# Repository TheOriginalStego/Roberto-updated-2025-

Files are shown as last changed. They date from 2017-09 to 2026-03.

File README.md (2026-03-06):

# Roberto

Roberto during Vivapoly 2014

This is the program that runs in Roberto, the pastis serving robot of [Robopoly](http://robopoly.epfl.ch) made by Steven Roelofsen.

The program runs on a white version of the [PRismino](https://github.com/Robopoly/PRismino) that is attached to the front of the robot. It needs the [`robopolyLCD`
](https://github.com/Robopoly/LCD-module) library for the LCD.

## Configuration

The program has been made so the robot could be configured live via the USB port, options that can be changed are: quantity of poured liquid, type of liquid (pastis or syrup) and method of serving (immediate or wait for button press).

There are 2 configurations for the robot, it usually server either syrup during non-alcoholic manifestations and then pastis during Vivapoly, the last big event of an academic year at EPFL.

Configuration commands:

| Command | Action | Parameters 			|
|---|---|---|
| 1 | Set new pouring weight | n (pouring weight in g, int) 			|
| 2 | Check configuration | 			|
| 3 | Read how many times the pump has been activated | 			|
| 4 | Show sensor values | 			|
| 5 | Change mode | 0 = automatic, 1 = manual 			|
| 6 | Change type | 0 = Ricard, 1 = syrup (unused) 	|
| 7 | Enable debug mode | 			|

So for example to set the pouring time the user first sends `1` to select the command and then sends the pouring time in milliseconds (ex: `2000`).

## Memory

Some information is stored in EEPROM to save it even when the robot is power cycled: drinks served, pouring time in milliseconds, serving type and serving mode. Drinks served and pouring time can be consulted at any time by pushing on the arm touch sensor on the right arm, the values will be shown on the front LCD.

## State machine

The program follows strictly a simple state machine that is very easy to manage:

Roberto finite state machine

In idle mode, while waiting for a cup to be inserted or removed, it moves and toggles its various servomotors and lights randomly to attract attention.

## Debug mode

The debug mode allows to enter a special mode that lets the user toggle on or off the lights, pump and show the sensor status on the LCD screen. To exit this mode the MCU has to be reset using the on-board button in front of the robot.

## Hardware design

The ears and hands are 3d printed. Only the ears are available as the others have gone lost (or unusable designs). The ears are identical and can easily be 3d printed.

The power system has been revised in May 2016, leading to the design of a new pump drive PCB featuring a MOSFET transistor. DC 5V regulation is now performed by Robopoly’s Power-Board instead of not-so-efficient linear regulators.

In 2017, a second pump was added. The pumps are driven by having stacked PCBs from 2016. Furthermore, a shield made from veroboard was made. It works as a normal shield instead of an "inverted shield". This way if the Prismino dies, any other can be used. 
Also, the amount of liquid to be poured is now measured using a scale instead of a timer (ie no measurement). This required the hand to be redesigned and the design can be found on the Fusion360 account of Robopoly.

## CHANGELOG
### 2025 Maintenance and repair
In may 2025, repair and maintenance was done by Tibor Truong.
The design of both hands was modified in order to adapt to various sizes of glasses and improve reliability. The loadcell was removed from it's plattform underneath the cup holder and was integrated directly into the cup holder (holder itself measures the weight). The hand on the "pouring" side was also redesigned. The hoses can now be installed and removed way faster thanks to zipties.
The switch that sensed the closing of the hands was replaced by a reed sensor. This ensures that contact is closed even when the arms don't touch very well (due to mechanical play).
The existing two pumps were thoroughly cleaned with a 1% NaOH solution to get rid of the mold and other gunk that has been building up for years.
During repair, the loadcell amplifier board was damaged, it got replaced by a more recent model sold by Robopoly.

Note for users: Please always rince the hoses at least with warm water (or better with a desinfecting solution) and dry them completely before putting away the robot for storage. Leaving liquids in the pumps and hoses leads to mold formation and it's very work intensive to get rid of it again. Not even mentioning that it's disgusting and not foodsafe.

## Credits

This project has been an ongoing one and a lot of people have been working on it without whom this wonderful robot would've never existed.

| Contribution | Name 										|
|---|---|
| Creator | Steven Roelofsen 										|
| Programmers | Karl Kangur, Taavet Kangur, Patrick Bobbink								|
| Electronics | Marco Pagnamenta, Benjamin Bonnal, Paul-Edouard Sarlin, Patrick Bobbink 	|
| Cabling, mechanics | Lobsang Blanchard, Patrick Bobbink				 				|

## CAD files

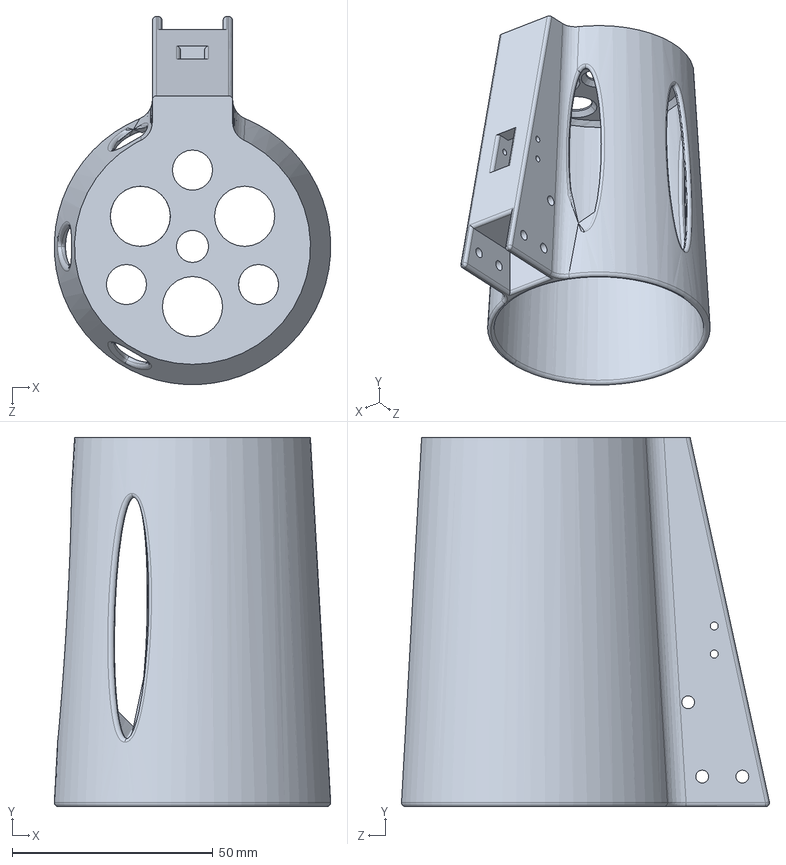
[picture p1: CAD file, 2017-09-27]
Hardware/Hand_second_version/sld/main_verre1.SLDPRT
68.8 x 92.0 x 91.7 mm

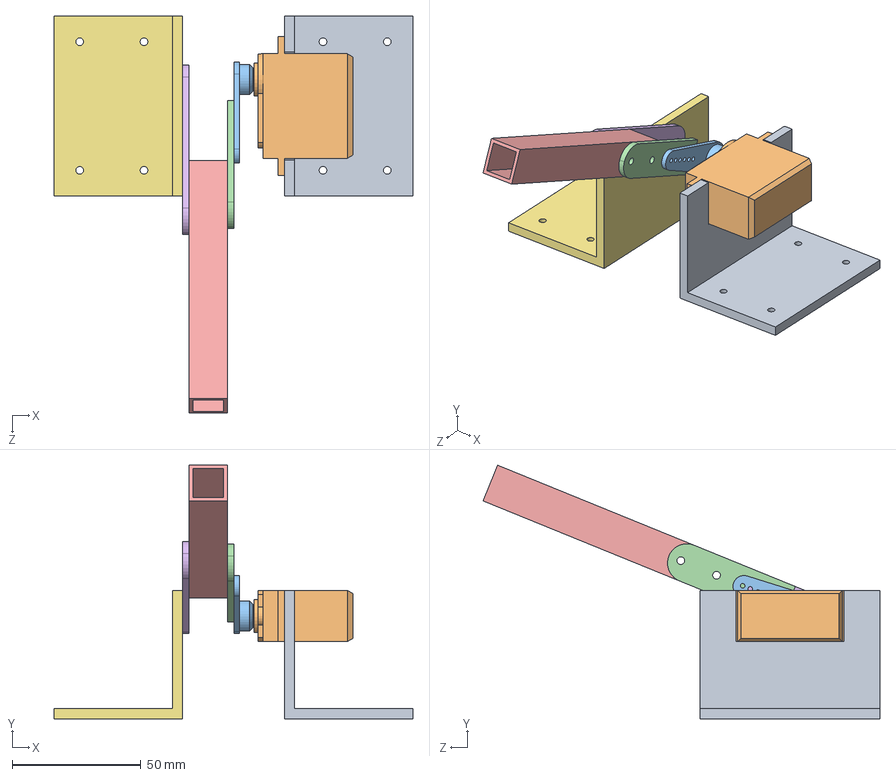
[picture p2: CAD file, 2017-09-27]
Hardware/Initial_robot_design/source/R_S_asm_bras_droit.SLDASM
139.6 x 98.6 x 154.4 mm
profilé_L_grand_servo
servomoteur
servomoteur_plateau_1
plaquette_bras_servo
profilé_carré_creux_1
plaquette_bras_pivot
profilé_L_grand2

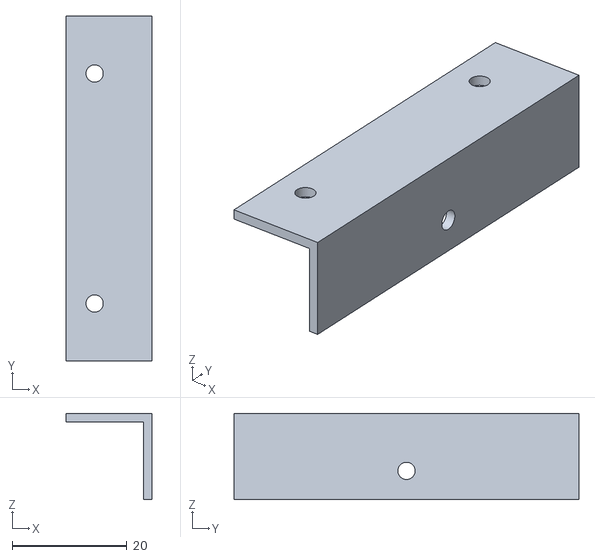
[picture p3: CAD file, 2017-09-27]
Hardware/Initial_robot_design/stl/R_S_asm_1 - R_S_asm_tete-1 profilé_L_tete-3.STL
15.0 x 60.0 x 15.0

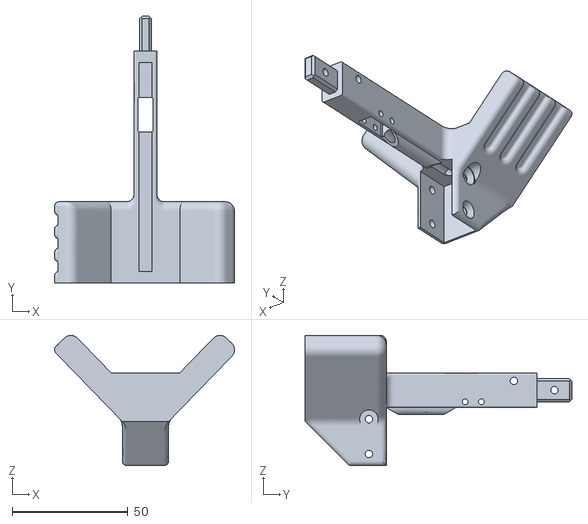
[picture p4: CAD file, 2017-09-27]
Hardware/Hand_second_version/stl/main_tuyau.STL
77.6 x 115.0 x 56.1

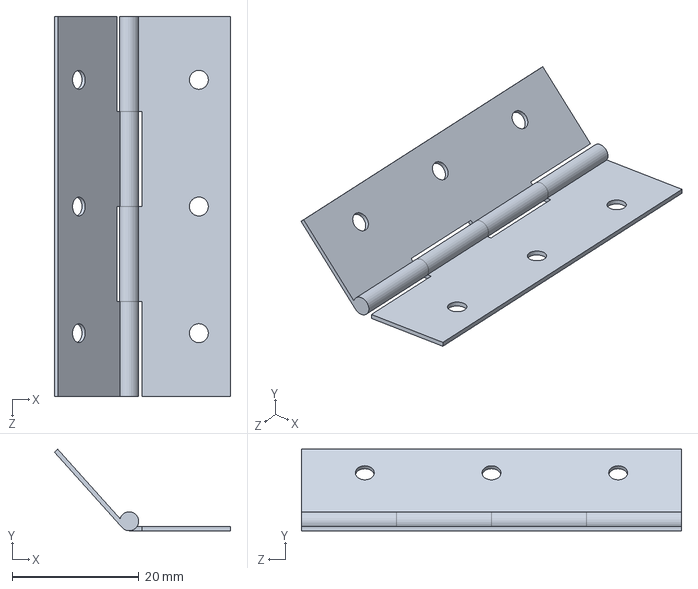
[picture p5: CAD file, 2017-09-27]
Hardware/Initial_robot_design/source/charnière_asm.SLDASM
27.8 x 12.9 x 60.0 mm
charnière_bras_1 x 2

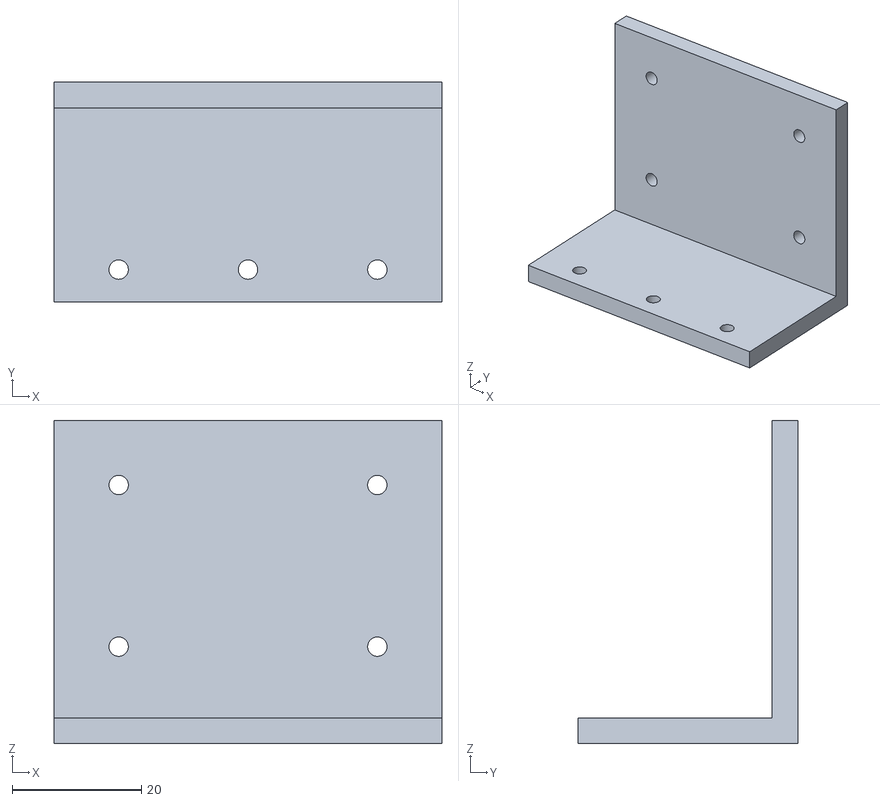
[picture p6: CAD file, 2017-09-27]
Hardware/Initial_robot_design/stl/R_S_asm_1 - R_S_asm_bras_droit2-1 profilé_L_grand4-1.STL
60.0 x 34.0 x 50.0

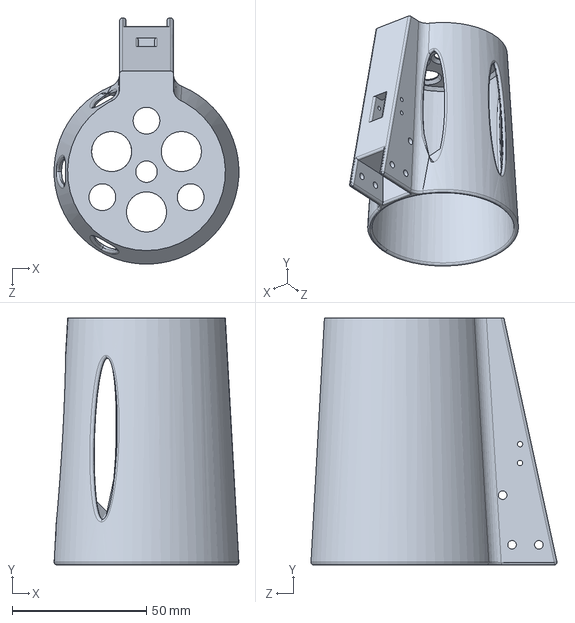
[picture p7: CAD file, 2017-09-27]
Hardware/Hand_second_version/sld/asm_verre_main.SLDASM
68.8 x 92.0 x 91.7 mm
main_verre1
levier

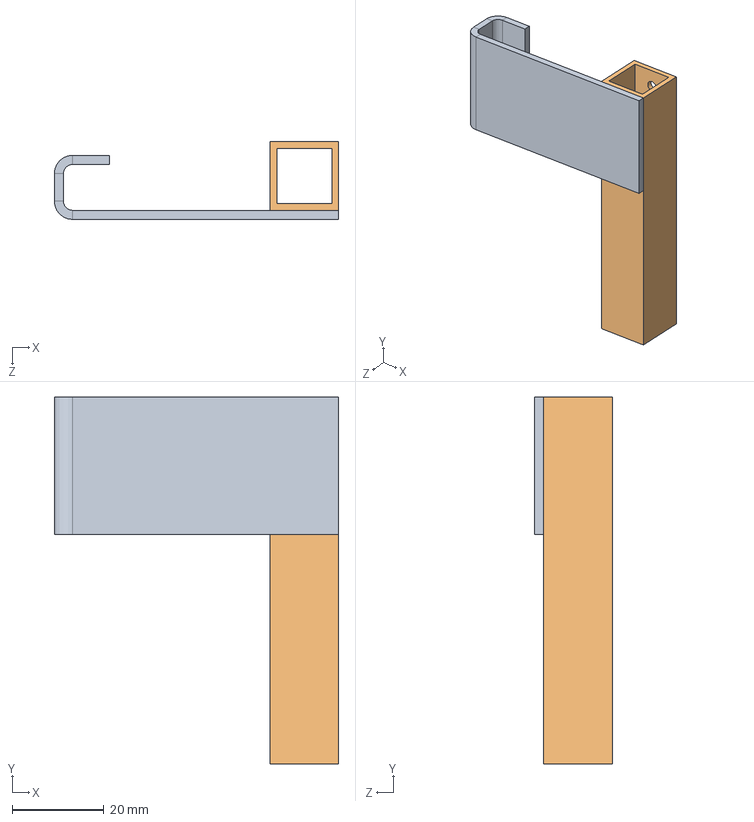
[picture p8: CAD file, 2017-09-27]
Hardware/Initial_robot_design/source/R_S_asm_vanne.SLDASM
62.0 x 80.0 x 17.0 mm
plaque_vanne1
profilé_carré_creux_5

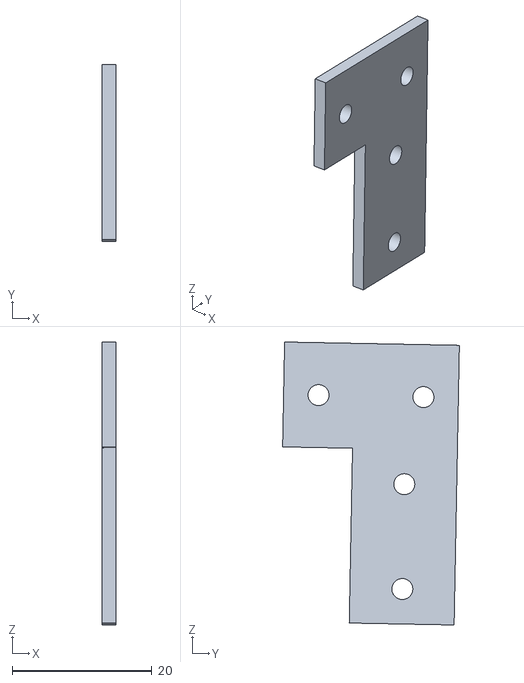
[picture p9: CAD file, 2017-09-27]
Hardware/Initial_robot_design/stl/R_S_asm_1 - plaquette_attache_bras-8.STL
2.06 x 25.3 x 40.5

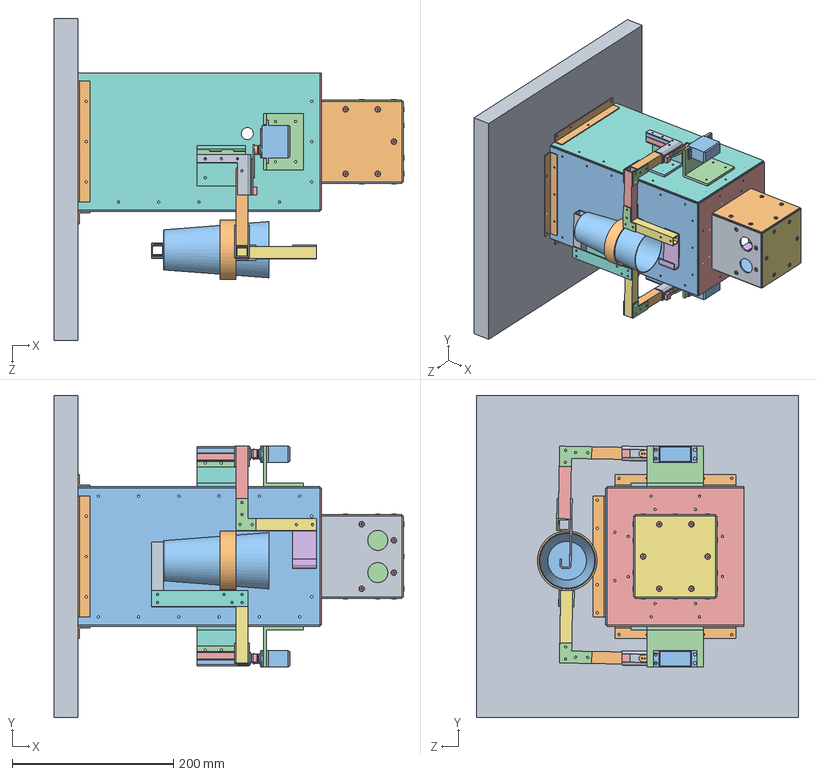
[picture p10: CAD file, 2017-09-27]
Hardware/Initial_robot_design/source/R_S_asm_1.SLDASM
434.6 x 400.0 x 400.0 mm
socle
profilé_L_socle x 3
plaque_devant
profilé_L_haut_coté x 3
plaque_haut
profilé_L_haut_tete x 4
plaque_tete_haut
profilé_L_tete x 8
plaque_tete_devant
plaque_tete_D
plaque_tete_G
plaque_tete_arriere
rivet_pop_3.5mm x 24
profilé_L_coté x 2
plaque_droite
plaque_gauche
tole_bras_1 x 2
profilé_carré_creux_8 x 2
cale_bras_1 x 2
charnière_bras_1 x 4
cale_bras_2 x 2
aimant_12x12x12 x 2
aimant_10x10x1 x 2
profilé_L_grand4 x 2
servo_aimant_1 x 2
servomoteur_plateau_1 x 2
servomoteur x 2
profilé_L_grand_servo x 2
aimant_10x10x5 x 2
plaquette_caoutchouc x 2
profilé_carré_creux_3
porte_verre_plaquette x 2
profilé_carré_creux_4
anneau_porte_verre2
verre1
plaquette_attache_bras x 6
profilé_carré_creux_6
plaque_vanne1
profilé_carré_creux_5

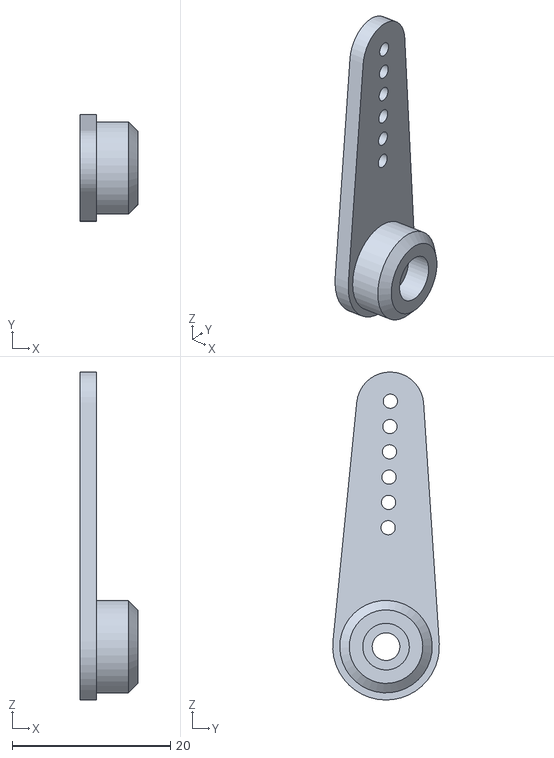
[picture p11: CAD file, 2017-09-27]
Hardware/Initial_robot_design/stl/R_S_asm_1 - R_S_asm_bras_droit2-1 servomoteur_plateau_1-1.STL
7.30 x 13.5 x 41.5

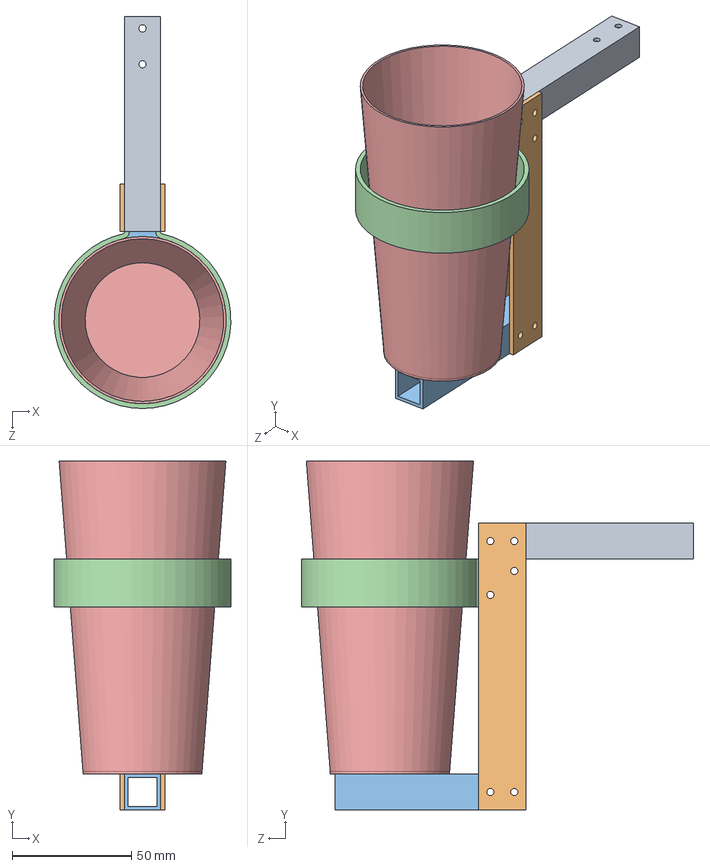
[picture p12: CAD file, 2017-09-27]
Hardware/Initial_robot_design/source/R_S_asm_porte_verre.SLDASM
73.9 x 146.0 x 164.0 mm
profilé_carré_creux_3
porte_verre_plaquette x 2
profilé_carré_creux_4
anneau_porte_verre2
verre1

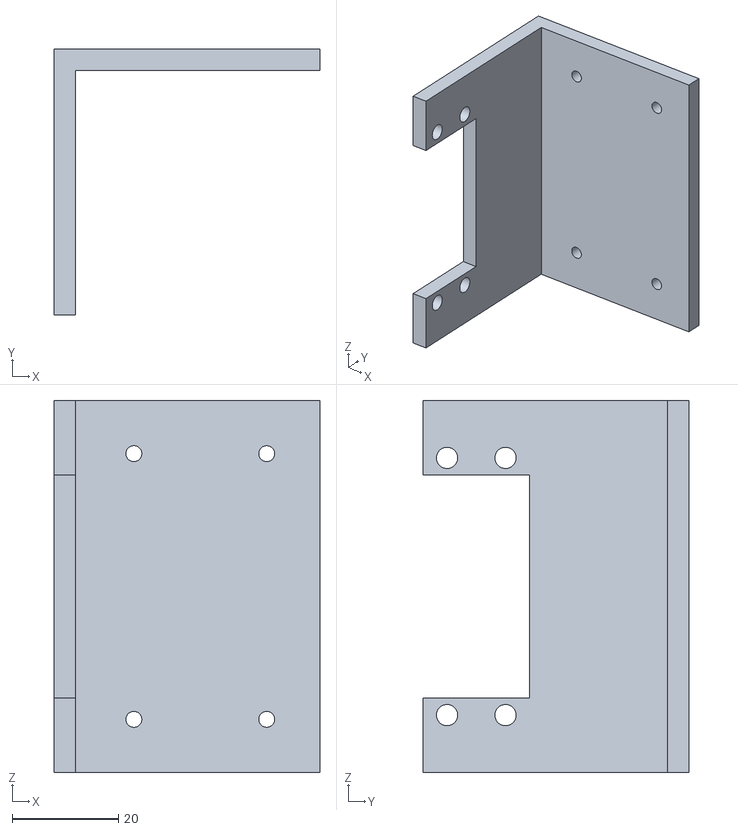
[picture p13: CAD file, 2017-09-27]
Hardware/Initial_robot_design/stl/R_S_asm_1 - R_S_asm_bras_droit2-1 profilé_L_grand_servo-1.STL
50.0 x 50.0 x 70.0

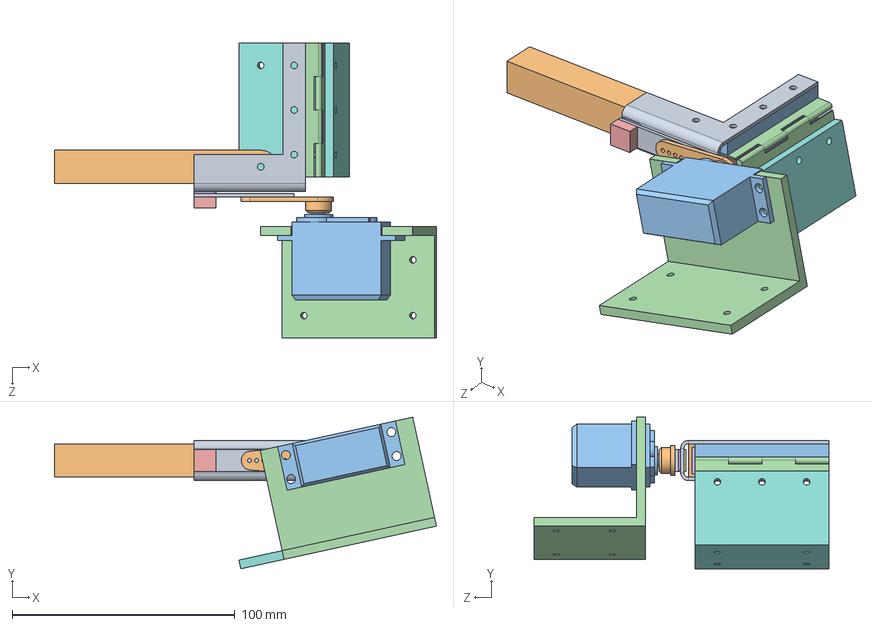
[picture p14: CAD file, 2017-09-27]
Hardware/Initial_robot_design/source/R_S_asm_bras_gauche2.SLDASM
171.3 x 68.0 x 132.2 mm
tole_bras_1
profilé_carré_creux_8
cale_bras_1
charnière_bras_1 x 2
cale_bras_2
aimant_12x12x12
aimant_10x10x1
profilé_L_grand4
servo_aimant_1
servomoteur_plateau_1
servomoteur
profilé_L_grand_servo
aimant_10x10x5
plaquette_caoutchouc

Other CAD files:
Hardware/Hand_second_version/stl/main_verre.STL
Hardware/Initial_robot_design/stl/R_S_asm_1 - R_S_asm_tete-1 rivet_pop_3.5mm-4.STL
Hardware/Initial_robot_design/source/servo_asm.SLDASM
Hardware/Initial_robot_design/stl/R_S_asm_1 - R_S_asm_bras_droit2-1 aimant_10x10x5-1.STL
Hardware/Hand_second_version/sld/levier.SLDPRT
Hardware/Hand_second_version/stl/levier.stl
Hardware/Hand_second_version/stl/levier2.STL
Hardware/Hand_second_version/stl/pince_tuyau.stl
Hardware/Initial_robot_design/source/R_S_asm_bras_droit2.SLDASM
Hardware/Initial_robot_design/source/R_S_asm_bras_gauche.SLDASM
Hardware/Initial_robot_design/source/R_S_asm_tete.SLDASM
Hardware/Initial_robot_design/source/aimant_10x10x1.SLDPRT
Hardware/Initial_robot_design/source/aimant_10x10x5.SLDPRT
Hardware/Initial_robot_design/source/aimant_12x12x12.SLDPRT
Hardware/Initial_robot_design/source/anneau_porte_verre1.SLDPRT
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

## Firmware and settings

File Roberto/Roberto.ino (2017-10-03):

/***************************************************************************************
 *
 * Title:       Roberto, the pastis serving robot
 * Version:     v1.1
 * Date:        2017-07-17
 * Author:      Karl Kangur <karl.kangur@gmail.com>
 * Website:     https://github.com/Robopoly/Roberto
 * Licence:     LGPL
 *
 ***************************************************************************************/
#include <Servo.h>
#include <Wire.h>
#include <EEPROM.h>
#include "Roberto.h"
#include <robopolyLCD.h>
#include "HX711.h"        //for the loadcell : https://learn.sparkfun.com/tutorials/load-cell-amplifier-hx711-breakout-hookup-guide

Servo servoEarLeft;
Servo servoEarRight;
Servo servoBowTie;
Servo servoArmLeft;
Servo servoArmRight;

// buffer for user input
char buffer[16];

// transition structure
struct transition
{
    enum state_codes state_source;
    enum return_codes return_code;
    enum state_codes state_destination;
};

// state functions and codes must be in sync
return_codes (*state[])(void) = {
  stateWaitingCup,
  stateMovingArmsIn,
  statePouring,
  stateMovingRightArmOut,
  stateRemoveCup,
  stateMovingArmsOut
};

struct transition state_transitions[] = {
  {STATE_WAITING_CUP,          OK,     STATE_MOVING_ARMS_IN},
  {STATE_WAITING_CUP,          REPEAT, STATE_WAITING_CUP},
  {STATE_MOVING_ARMS_IN,       OK,     STATE_POURING},
  {STATE_MOVING_ARMS_IN,       FAIL,   STATE_MOVING_ARMS_OUT},
  {STATE_POURING,              OK,     STATE_MOVING_RIGHT_ARM_OUT},
  {STATE_POURING,              FAIL,   STATE_MOVING_ARMS_OUT},
  {STATE_MOVING_RIGHT_ARM_OUT, OK,     STATE_REMOVE_CUP},
  {STATE_REMOVE_CUP,           OK, STATE_MOVING_ARMS_OUT},
  {STATE_REMOVE_CUP,           REPEAT, STATE_REMOVE_CUP},
  {STATE_MOVING_ARMS_OUT,      OK,     STATE_WAITING_CUP}
};

enum state_codes currentState;
enum return_codes returnCode;

// pointer to the current called function in the state machine
return_codes (*stateFunction)(void);

// time from start of liquid pouring in milliseconds
uint16_t pouredWeight;
uint8_t liquidType;
uint8_t servingMode;
uint8_t debugMode;

HX711 scale(INPUT_SCALE_DAT, INPUT_SCALE_CLK);            //!!!!!!!!

float calibration_factor = 6260;                //Calibration factor found by test on the SparkFun Calibration program ///!!!!!!!!

bool pastis;

void setup()
{
/*
Serial.begin(9600);
  pinMode(OUTPUT_PUMP_1, OUTPUT);
  pinMode(OUTPUT_PUMP_2, OUTPUT);
  pinMode(OUTPUT_EYE_LEFT_RED, OUTPUT);
  pinMode(OUTPUT_EYE_LEFT_GREEN, OUTPUT);
  pinMode(OUTPUT_EYE_LEFT_BLUE, OUTPUT);
  pinMode(OUTPUT_EYE_RIGHT_RED, OUTPUT);
  pinMode(OUTPUT_EYE_RIGHT_GREEN, OUTPUT);
  pinMode(OUTPUT_EYE_RIGHT_BLUE, OUTPUT);
  while(1)
  {
    if(COND_BUTTON_1_PRESSED)
    {
        MACRO_PUMP_1_ON;
        delay(1000);
        MACRO_PUMP_1_OFF;
        Serial.println("button 1");
    }
    else if (COND_BUTTON_2_PRESSED)
    {
      eyes(1,1,1);
       // MACRO_PUMP_2_ON;
        delay(1000);
       // MACRO_PUMP_2_OFF;
       eyes(0,0,0);
       Serial.println("button 2");
    }
    delay(100);
  }
  */

/* Serial.begin(9600);
 scale.tare();
 scale.set_scale(calibration_factor);
 while(1)
 {
  Serial.println(SCALE_VALUE);
  delay(500);
 }*/
/*// ******************************************************** BEGIN DEBUG ************************************** !!!!!!
 Serial.begin(9600);
  // set port modes
//  pinMode(LED, OUTPUT);
  pinMode(OUTPUT_PUMP, OUTPUT);
  pinMode(OUTPUT_EYE_LEFT_RED, OUTPUT);
  pinMode(OUTPUT_EYE_LEFT_GREEN, OUTPUT);
  pinMode(OUTPUT_EYE_LEFT_BLUE, OUTPUT);
  pinMode(OUTPUT_EYE_RIGHT_RED, OUTPUT);
  pinMode(OUTPUT_EYE_RIGHT_GREEN, OUTPUT);
  pinMode(OUTPUT_EYE_RIGHT_BLUE, OUTPUT);
  pinMode(INPUT_ARM_CONTACT, INPUT);
  digitalWrite(OUTPUT_EYE_LEFT_RED, HIGH);
  digitalWrite(OUTPUT_EYE_LEFT_GREEN, LOW);
  digitalWrite(OUTPUT_EYE_LEFT_BLUE, LOW);
  digitalWrite(OUTPUT_EYE_RIGHT_RED, HIGH);
  digitalWrite(OUTPUT_EYE_RIGHT_GREEN, LOW);
  digitalWrite(OUTPUT_EYE_RIGHT_BLUE, LOW);
  delay(1000);
  eyes(0,1,0);
  delay(1000);
  eyes(0,0,1);
servoArmLeft.attach(OUTPUT_SERVO_ARM_LEFT);
servoArmLeft.write(SERVO_ARM_LEFT_OPEN);
servoArmRight.attach(OUTPUT_SERVO_ARM_RIGHT);
servoArmRight.write(SERVO_ARM_RIGHT_OPEN);
servoBowTie.attach(OUTPUT_SERVO_BOWTIE);
servoBowTie.write(SERVO_BOWTIE_CENTER);
delay(200);
servoBowTie.write(SERVO_BOWTIE_LEFT);
delay(1000);
servoBowTie.write(SERVO_BOWTIE_RIGHT);
servoEarRight.attach(OUTPUT_SERVO_RIGHT_EAR);
servoEarRight.write(SERVO_EAR_RIGHT_CENTER);
delay(200);
servoEarRight.write(SERVO_EAR_RIGHT_FORWARDS);
delay(1000);
servoEarRight.write(SERVO_EAR_RIGHT_BACK);
servoEarLeft.attach(OUTPUT_SERVO_LEFT_EAR);
servoEarLeft.write(SERVO_EAR_LEFT_CENTER);
delay(200);
servoEarLeft.write(SERVO_EAR_LEFT_FORWARDS);
delay(1000);
servoEarLeft.write(SERVO_EAR_LEFT_BACK);
MACRO_PUMP_ON;
delay(500);
MACRO_PUMP_OFF;
while(1)
{
  Serial.println(COND_ARMS_TOUCH);
}
  while(1)
  ;
// ******************************************************** END DEBUG ************************************** !!!!!!  */


  pinMode(OUTPUT_PUMP_1, OUTPUT);
  pinMode(OUTPUT_PUMP_2, OUTPUT);
  pinMode(OUTPUT_EYE_LEFT_RED, OUTPUT);
  pinMode(OUTPUT_EYE_LEFT_GREEN, OUTPUT);
  pinMode(OUTPUT_EYE_LEFT_BLUE, OUTPUT);
  pinMode(OUTPUT_EYE_RIGHT_RED, OUTPUT);
  pinMode(OUTPUT_EYE_RIGHT_GREEN, OUTPUT);
  pinMode(OUTPUT_EYE_RIGHT_BLUE, OUTPUT);

  pinMode(INPUT_ARM_CONTACT, INPUT);
  pinMode(INPUT_BUTTON_1, INPUT);
  pinMode(INPUT_BUTTON_2, INPUT);
  // light up the eyes in red (debug)
  eyes(1, 0, 0);

  
  
  // set up serial communication for debug and configuration
  Serial.begin(9600);
  
  // configure servo motors
  servoArmLeft.attach(OUTPUT_SERVO_ARM_LEFT);
  servoArmRight.attach(OUTPUT_SERVO_ARM_RIGHT);
  servoBowTie.attach(OUTPUT_SERVO_BOWTIE);
  servoEarRight.attach(OUTPUT_SERVO_RIGHT_EAR);
  servoEarLeft.attach(OUTPUT_SERVO_LEFT_EAR);
  
  // initialise servo positions
  servoArmLeft.write(SERVO_ARM_LEFT_OPEN);
  servoArmRight.write(SERVO_ARM_RIGHT_OPEN);
  servoBowTie.write(SERVO_BOWTIE_CENTER);
  servoEarRight.write(SERVO_EAR_RIGHT_CENTER);
  servoEarLeft.write(SERVO_EAR_LEFT_CENTER);
  

  
  // load data from memory
  pouredWeight = (EEPROM.read(EEPROM_POURING_TIME) << 8) | EEPROM.read(EEPROM_POURING_TIME + 1);
  liquidType = EEPROM.read(EEPROM_TYPE);
  servingMode = EEPROM.read(EEPROM_MODE);


  // check the values we just read...
  if(pouredWeight < 0 || pouredWeight > MAX_POURED_WEIGHT)
    pouredWeight = DEFAULT_POURED_WEIGHT;

  if(liquidType < 0 || liquidType > 1)
    liquidType = 0;
  if(servingMode != 0 && servingMode != 1)
    servingMode = 1;

  
  // start i2c bus for LCD screen
  Wire.begin();
  
  // initialise LCD screen
  lcd("Initialising", "systems...");
  
  // initialise robot state
  currentState = ENTRY_STATE;
  
  // no debug mode
  debugMode = 0;
  
  // normal eye color
  eyes(0, 1, 1);

  //Reset the scale to 0
  scale.tare(); 

  MACRO_PUMP_1_OFF;
  MACRO_PUMP_2_OFF;
}

void loop()
{
  scale.set_scale(calibration_factor);  //Adjust to this calibration factor
  
  // debug mode shows the sensor values on lcd
  if(debugMode != 0)
  {
    if(debugMode == 1)
    {
      // detach servo motors so that they could be moved freely
      servoArmLeft.detach();
      servoArmRight.detach();
      servoBowTie.detach();
      servoEarRight.detach();
      servoEarLeft.detach();
  
      debugMode = 2;
    }
    
    if(Serial.available())
    {
      char c = Serial.read();
      while(Serial.available())
      {
        Serial.read();
      }
      switch(c)
      {
        case '1':
          Serial.println("Pump on");
          MACRO_PUMP_1_ON;
          break;
        case '2':
          Serial.println("Pump off");
          MACRO_PUMP_1_OFF;
          break;
        case '3':
          Serial.println("LEDs on");
          eyes(1, 1, 1);
          break;
        case '4':
          Serial.println("LEDs off");
          eyes(0, 0, 0);
          break;
        default:
          Serial.println("Debug mode:\n1: pump on\n2: pump off\n3: leds on\n4: leds off\nReset MCU to quit");
      }
    }
    String line1 = "CUP: ";
//    line1 += digitalRead(INPUT_CUP);
//    line1 += ", FLOW: ";
//    line1 += digitalRead(INPUT_FLOW);
    
    String line2 = "BTN: ";
    line2 += digitalRead(INPUT_BUTTON_1);
    line2 += ", TOUCH: ";
    line2 += digitalRead(INPUT_ARM_CONTACT);
    
    lcd(line1.c_str(), line2.c_str());
    delay(200);
    Serial.println(debugMode);
    return;
  }
  // current function to call according to the state machine
  stateFunction = state[currentState];
  // actually call the function
  returnCode = stateFunction();
  // fetch next state
  currentState = lookupTransitions(currentState, returnCode);
  
  if(Serial.available())
  {
    char c = Serial.read();
    while(Serial.available())
    {
      Serial.read();
    }
    switch(c)
    {
      // clear input (typically the remaining "\n" character)
      case '1':
                                                                                                //need NEW make pouringTime Into Loadcell value
        // clear the input buffer
        memset(buffer, 0, sizeof(buffer));
        // wait for user input, 16 character or 15 and a "\n" termination character
        Serial.setTimeout(5000);
        Serial.println("Enter new pouring weight in grams");
        Serial.readBytesUntil('\n', buffer, 15);
        pouredWeight = atoi(buffer);
        EEPROM.write(EEPROM_POURING_TIME, pouredWeight >> 8);
        EEPROM.write(EEPROM_POURING_TIME + 1, pouredWeight & 0xff);
        Serial.print("New pouring weight set ");
        Serial.print(pouredWeight);
        Serial.println(" g");
        Serial.setTimeout(1000);
        break;
      case '2':
                                                                                                      //need NEW make pouringTime Into Loadcell value
        Serial.print("Current pouring weight: ");
        Serial.print((EEPROM.read(EEPROM_POURING_TIME) << 8) | EEPROM.read(EEPROM_POURING_TIME + 1));
        Serial.println(" g");
        Serial.print("Serving mode: ");
        Serial.println(EEPROM.read(EEPROM_MODE));
        Serial.print("Serving type: ");
        Serial.println(EEPROM.read(EEPROM_TYPE));
        break;
      case '3':
        Serial.print("The pump has been activated ");
        Serial.print((EEPROM.read(EEPROM_PUMP_ACTIVATION) << 8) | EEPROM.read(EEPROM_PUMP_ACTIVATION + 1));
        Serial.println(" times");
        break;
      case '4':
        Serial.print("Sensors: CUP=");
    //    Serial.print(digitalRead(INPUT_CUP));
        Serial.print(", ARM_CONTACT=");
        Serial.print(digitalRead(INPUT_ARM_CONTACT));
 //      Serial.print(", FLOW=");
 //       Serial.println(digitalRead(INPUT_FLOW));
        break;
      case '5':
        Serial.println("Change serving mode: 0 = manual (must click on button), 1 = automatic");
        memset(buffer, 0, sizeof(buffer));
        Serial.setTimeout(5000);
        Serial.readBytesUntil('\n', buffer, 15);
        servingMode = atoi(buffer);
        EEPROM.write(EEPROM_MODE, servingMode);
        Serial.println("New serving mode set");
        Serial.setTimeout(1000);
        break;
      case '6':
                                                                                                      //need NEW No types or new state 2 where multiple cocktails are available
        Serial.println("Change liquid type: 0 = Ricard, 1 = syrup");
        memset(buffer, 0, sizeof(buffer));
        Serial.setTimeout(5000);
        Serial.readBytesUntil('\n', buffer, 15);
        liquidType = atoi(buffer);
        EEPROM.write(EEPROM_TYPE, liquidType);
        Serial.println("New liquid type set");
        Serial.setTimeout(1000);
        break;
      case '7':
        Serial.println("Entering debug mode, reset MCU to quit.");
        debugMode = 1;
        break;
      default:
        Serial.println("Roberto configuration:\n1: set new pouring time\n2: check configuration\n3: read how many times the pump has been activated\n4: show sensor values\n5: change mode (automatic/manual)\n6: change type (Ricard, syrup)\n7: Enable debug mode");
    }
  }
}

// returns the new state according to the current state and the return value
state_codes lookupTransitions(state_codes state, return_codes code)
{
  uint8_t i;
  // default return state is the entry state
  state_codes nextState = ENTRY_STATE;
  // see if a state transition matches and switch to the next state
  for(i = 0; i < sizeof(state_transitions) / sizeof(transition); i++)
  {
    if(state_transitions[i].state_source == state && state_transitions[i].return_code == code)
    {
      nextState = state_transitions[i].state_destination;
      break;
    }
  }
  return nextState;
}

return_codes stateWaitingCup()
{
  // timer to animate the robot while idle
  static uint32_t lcdUpdateTime = 0;
  static uint8_t idleState = 0;
  if(millis() > lcdUpdateTime)
  {
    switch(idleState)
    {
      case 0:
        lcd("Salut, je suis", "Roberto");
        break;
      case 1:
        lcd("Le robot serveur", "de Robopoly");
        break;
      case 2:
                                                                                                      //need NEW case 2: two cocktails TYPE_COCKTAILS
        if(liquidType == TYPE_RICARD)
        {
          lcd("Je sers des", "boissons!");
        }
        else if(liquidType == TYPE_SYRUP)
        {
          lcd("Je sers du", "sirop");
        }
        break;
      case 3:                                                                                                //need NEW message for case 2

        if(liquidType == TYPE_RICARD)
        {
          lcd("Pour seulement", "7 petits francs");
        }
        else if(liquidType == TYPE_SYRUP)
        {
          lcd("Et c'est", "gratuit");
        }
        break;
    }

    
    Serial.println("State: waiting for cup");
    Serial.println("weight in cup holder ");
    Serial.print(SCALE_VALUE);
    Serial.print("  ");
    Serial.print(SCALE_VALUE > MIN_VAL_MASS_CUP_DETEC);
    // toggle the next state, modulo 4
    idleState = (idleState + 1) & 0b11;
    
    lcdUpdateTime = millis() + TIME_LCD_UPDATE;
  }
  
  if(COND_ARMS_TOUCH)
  {
    uint32_t configurationTextChangeDelay = 0;
    char message[16];
    uint8_t showConfigState = 0;
    while(COND_ARMS_TOUCH)
    {
      if(millis() > configurationTextChangeDelay)
      {
        switch(showConfigState)
        {
          case 0:
            itoa((EEPROM.read(EEPROM_PUMP_ACTIVATION) << 8) | EEPROM.read(EEPROM_PUMP_ACTIVATION + 1), message, 10);
            lcd(message, "fois servis");
            break;
          case 1:

            itoa(pouredWeight, message, 10);
            lcd(message, "masse a debiter");
            break;
        }
        showConfigState = (showConfigState + 1) & 1;
        
        configurationTextChangeDelay = millis() + TIME_LCD_UPDATE;
      }
    }
  }
  
  // a human blinks every 2 to 10 seconds and a blink is about 200ms in duration
  static uint32_t nextBlink = millis() + 2000 * random(1, 5);
  if(millis() > nextBlink)
  {
    eyes(0, 0, 0);
    delay(200);
    eyes(0, 1, 1);
    nextBlink = millis() + 2000 * random(1, 5);
  }
  
//  static uint32_t ledToggleTime = millis() + TIME_HEARTBEAT;
//  if(millis() > ledToggleTime)
//  {
    // toggle the onboard LED
//    digitalWrite(LED, !digitalRead(LED));
//    ledToggleTime = millis() + TIME_HEARTBEAT;
//  }
  
  static uint32_t bowTieMoveTime = millis() + TIME_BOWTIEMOVE * random(1, 10);
  if(millis() > bowTieMoveTime)
  {
    // toggle the onboard LED
    servoBowTie.write(random(SERVO_BOWTIE_LEFT, SERVO_BOWTIE_RIGHT));
    bowTieMoveTime = millis() + TIME_BOWTIEMOVE * random(1, 10);
  }
  
  // ear movement
  static uint32_t earMoveTime = millis() + TIME_EAR_MOVE_IDLE * random(1, 10);
  if(millis() > earMoveTime)
  {
    servoEarRight.write(random(min(SERVO_EAR_RIGHT_BACK, SERVO_EAR_RIGHT_FORWARDS), max(SERVO_EAR_RIGHT_BACK, SERVO_EAR_RIGHT_FORWARDS)));
    servoEarLeft.write(random(min(SERVO_EAR_LEFT_BACK, SERVO_EAR_LEFT_FORWARDS), max(SERVO_EAR_LEFT_BACK, SERVO_EAR_LEFT_FORWARDS)));
    
    earMoveTime = millis() + TIME_EAR_MOVE_IDLE * random(1, 10);
  }
  
  // fast disco mode
  static uint32_t discoModeTime = millis() + TIME_DISCO_MODE;
  static uint32_t discoModeDuration = discoModeTime + TIME_DISCO_DURATION;
  if(millis() > discoModeTime)
  {
    if(millis() < discoModeDuration)
    {
      eyesRandom();
    }
    else
    {
      eyes(0, 1, 1);
      discoModeTime = millis() + TIME_DISCO_MODE;
      discoModeDuration = discoModeTime + TIME_DISCO_DURATION;
    }
  }
  
  if(SCALE_VALUE > MIN_VAL_MASS_CUP_DETEC)                    //!!!
  {
    // turn eyes white
    eyes(1, 1, 1);
    pastis = 0;
    servoEarLeft.write(SERVO_EAR_LEFT_CENTER);
    servoEarRight.write(SERVO_EAR_RIGHT_CENTER);
    
    if(servingMode == MODE_MANUAL)
    {
      lcd("Goblet insere", "Payer l'humain");
      while(!COND_BUTTON_1_PRESSED)
      {
        pastis = 1;
        if(COND_BUTTON_2_PRESSED)
        {
          pastis = 0;
          Serial.println("Button 2 has been pressed.");
          return OK;
        }
        if(!(SCALE_VALUE > MIN_VAL_MASS_CUP_DETEC))
        {
          return REPEAT;
        }
      }
      // the cup was removed so simply return to the idle state
      return OK;
    }
    else if(servingMode == MODE_AUTOMATIC)
    {
      lcd("Goblet insere", "");
      return OK;
    }
  }
  return REPEAT;
}
return_codes stateMovingArmsIn()
{
  Serial.println("State: moving arms in");

  if(pastis == 1)
  {
    lcd("Et un Ricard", "un vrai!");
  }
  else if(pastis == 0)
  {
    lcd("Et voila un bon", "sirop!");
  }
  // do not move right away
  uint32_t waitAfterCut = millis() + TIME_WAIT_AFTER_CUP_INSERT;
  while(waitAfterCut > millis())
  {
    if(!(SCALE_VALUE > MIN_VAL_MASS_CUP_DETEC))
    {
      lcd("Erreur: goblet", "enleve");
      Serial.println("Error: cup was removed");
      return FAIL;
    }
  }
  // move arms in
  moveArmServo(servoArmLeft, SERVO_ARM_LEFT_CLOSED, SERVO_ARM_SPEED);
  moveArmServo(servoArmRight, SERVO_ARM_RIGHT_CLOSED, SERVO_ARM_SPEED);
  
  uint32_t timeout = millis() + 3000;
  while(!COND_ARMS_TOUCH)
  {
    // arms can be blocked, so a timeout is needed
    if(millis() > timeout)
    {
      lcd("Erreur: capteur", "bras");
      Serial.println("Error: timeout while moving arms in");
      return FAIL;
    }
    
    if(!(SCALE_VALUE > MIN_VAL_MASS_CUP_DETEC))
    {
      lcd("Erreur: goblet", "enleve");
      Serial.println("Error: cup was removed");
      return FAIL;
    }
  }
  
  return OK;
}

return_codes statePouring()
{
  // the liquid has reached the flow sensor, start timing, make sure cup is still there
  uint32_t start = millis();
//  uint32_t time = start + pouringTime;
  uint32_t bowTieTime = start + TIME_BOWTIE_TOGGLE;
  uint32_t now;
  uint8_t percent;
  char progress[4];
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

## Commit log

2017-09-27 Added the initial hardware source files. Not everything went according to plan, but it is mostly there.
    [R_S_asm_1 - R_S_asm_bras_droit2-1 aimant_10x10x1-1.STL, R_S_asm_1 - R_S_asm_bras_droit2-1 aimant_10x10x5-1.STL, R_S_asm_1 - R_S_asm_bras_droit2-1 aimant_12x12x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]
2025-05-21 README.md updated with an „CHANGELOG“ section to document recent mods
2026-03-06 New hand design
    Added a reed switch and relocated the load cell. New design accepts a wider variety of glasses than the previous model.
    [Roberto_New_Hands_2025.stl]
